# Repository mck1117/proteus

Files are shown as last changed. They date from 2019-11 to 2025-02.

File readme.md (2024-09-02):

# PROTEUS

_protean: able to do many different things; versatile._

A high-featured board compatible with [rusEFI](https://github.com/rusefi/rusefi) firmware.

TL;DR [Proteus Manual](https://github.com/rusefi/rusefi/wiki/Proteus-Manual)

# Goals and Non-Goals

## Goals

- Run my LS-swapped Volvo 240 with factory harness and equipment
- Run a sequential ignition, quad-VVT v12 engine (twelve injectors, twelve ignition, five hall sensors, four VVT actuators, dual throttles)
- Easily manufactured sealed enclosure (all connectors mount in-plane)
- ~~Extensible for knock sensing~~ properly implemented onboard knock sensing!

## Non-goals

- ~Internal logging (doesn't make sense with 12 mbit/s USB, and a sealed enclosure)~ Version 0.4 has an SD card!
- Direct injection
- Cheap

# Hardware Features

## Microcontroller

- STM32F429ZG
    - 180 MHz ARM Cortex-M7
    - 1MB flash
    - 256 KB SRAM
    - LQFP144 package

- Also fully compatible with several STM32F7 parts, including the STM32F767ZI, used on v0.1 and v0.2, as well as STM32F429ZIT6.

## Connectors
TE Connectivity AMPSEAL connectors:

- 2x 35 pin connectors
    - Board: TE 776231-1 (black, right) and 776231-2 (white, left)
    - Plug: TE 776164-1 (black, right) and 776164-2 (white, left)
- 1x 23 pin connector
    - Board: TE 776228-1
    - Plug: TE 770680-1
- 770854-1 terminals    

## Connectivity

- 1 mbit/s CAN bus
- USB 2.0 full speed (12 mbit/s), on-board or wired to connector for sealed applications
- [10-pin, 1.27mm Cortex debug header](http://infocenter.arm.com/help/topic/com.arm.doc.faqs/attached/13634/cortex_debug_connectors.pdf)

## Outputs
- 16x 4A low-side drivers
- 12x 5v ignition (or general purpose) outputs
- Dual H-bridges for electronic throttle (also supports stepper idle valve!)
- 4x 12v 3A high-side outputs

## Inputs

- 11x Analog voltage inputs
- 4x Analog temperature (5v pullup) inputs
- 2x VR crank/cam/vehicle speed inputs
- 6x hall cam/crank or digital input

## Power Supply

- Full operation from 6-24v supply
- Limited operation from 4-6v
- Dual 5v sensor supplies, 150mA each, fully protected
- Dual protected 12v external sensor supply

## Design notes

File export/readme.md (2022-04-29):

4 layer PCB

135mm x 82.5mm

[changelog.md](../changelog.md)

https://github.com/rusefi/rusefi/wiki/Hardware-Proteus-Fabrication

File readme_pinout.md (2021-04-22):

# Proteus Pinout & Wiring

### [Please use the official rusEfi Proteus docs here.](https://github.com/rusefi/rusefi/wiki/Proteus-Manual)

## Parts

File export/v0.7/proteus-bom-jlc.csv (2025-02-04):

Comment | Designator | Footprint | LCSC
Ferrite_Bead | FB1501 | Inductor_SMD:L_0805_2012Metric | C1015
8MHz | Y1501 | Crystal:Crystal_SMD_5032-2Pin_5.0x3.2mm | C115962
1k | R39,R41,R1217,R1218 | Resistor_SMD:R_0402_1005Metric | C11702
2.7k | R1101,R1102,R1103,R1104,R1201,R1202,R1203,R1204,R1401,R1402,R1403,R1404,R1405,R1406,R1407,R1408 | Resistor_SMD:R_0603_1608Metric | C13167
SM15T33CA | D1001 | Diode_SMD:D_SMC | C151281
330p | C23,C24,C905 | Capacitor_SMD:C_0402_1005Metric | C13533
10u | C18,C19,C27,C906,C1004,C1201 | Capacitor_SMD:C_1206_3216Metric | C13585
10u | L1001 | sunlord-MWSA0503:MWSA0503 | C408412
MIC4427 | U1602,U1603,U1701,U1702,U1801,U1802 | Package_SO:SOIC-8_3.9x4.9mm_P1.27mm | C20551
100n | C20,C701,C801,C901,C904,C1101,C1211,C1409,C1501,C1503,C1504,C1505,C1508,C1509,C1510,C1511,C1513,C1516,C1517,C1520,C1604,C1607,C1701,C1704,C1801,C1804 | Capacitor_SMD:C_0603_1608Metric | C14663
BTS4175SGA | U1102,U1103,U1104,U1105 | Package_SO:SOIC-8_3.9x4.9mm_P1.27mm | C152451
100n | C1,C2,C3,C4,C5,C6,C7,C8,C9,C10,C11,C12,C13,C14,C15,C16 | Capacitor_SMD:C_0402_1005Metric | C1525
33p | C1521,C1522 | Capacitor_SMD:C_0402_1005Metric | C1562
47p | C25,C26 | Capacitor_SMD:C_0402_1005Metric | C1567
1u | C1002,C1015,C1016,C1017,C1018,C1212,C1523 | Capacitor_SMD:C_0603_1608Metric | C15849
1n | C1204,C1205,C1207,C1208,C1209,C1210,C1401,C1402,C1403,C1404,C1405,C1406,C1407,C1408 | Capacitor_SMD:C_0603_1608Metric | C1588
680p | C21,C22 | Capacitor_SMD:C_0603_1608Metric | C1630
Micro_SD_Card | J1 | Connector_Card:microSD_HC_Wuerth_693072010801 | C164170
100 | R1601,R1602,R1603,R1604,R1701,R1702,R1703,R1704,R1801,R1802,R1803,R1804 | Resistor_SMD:R_0805_2012Metric | C17408
4.7k | R34,R35,R36,R37,R1205,R1206,R1208,R1209,R1210,R1211,R1213,R1214,R1215,R1216 | Resistor_SMD:R_0805_2012Metric | C17673
LMR14020 | U903 | Package_SO:SOIC-8-1EP_3.9x4.9mm_P1.27mm_EP2.29x3mm | C187824
4.7u | C30,C903,C1006,C1502,C1506,C1507,C1512,C1515 | Capacitor_SMD:C_0603_1608Metric | C19666
1k | RN201,RN202,RN301,RN302,RN401,RN402,RN501,RN502,RN1601,RN1701,RN1801 | Resistor_SMD:R_Array_Convex_4x0603 | C20197
Polyfuse | F101,F102 | Resistor_SMD:R_1206_3216Metric | C207035
120 | R33,R1004,R1106,R1108,R1110,R1112 | Resistor_SMD:R_0603_1608Metric | C22787
RED | D1504 | LED_SMD:LED_0603_1608Metric_Castellated | C2286
1 | R906 | Resistor_SMD:R_0402_1005Metric | C25086
82k | R1503 | Resistor_SMD:R_0603_1608Metric | C23254
2.2u | C1518,C1519 | Capacitor_SMD:C_0603_1608Metric | C23630
330 | R1508,R1509,R1510,R1511,R1512 | Resistor_SMD:R_0402_1005Metric | C25104
100k | R44,R45,R1501,R1901,R1902 | Resistor_SMD:R_0402_1005Metric | C25741
10k | R5,R6,R7,R8,R13,R14,R15,R16,R21,R22,R23,R24,R29,R30,R31,R32,R48,R905,R1001,R1006,R1007,R1105,R1107,R1109,R1111,R1502,R1504,R1513 | Resistor_SMD:R_0402_1005Metric | C25744
12k | R42,R43,R907 | Resistor_SMD:R_0402_1005Metric | C25752
33k | R38,R40,R46,R47 | Resistor_SMD:R_0402_1005Metric | C25779
470k | R701,R702,R703,R704,R801,R802,R803,R804,R901,R902,R903,R904,R1903,R1904 | Resistor_SMD:R_0402_1005Metric | C25790
5.6k | R1,R2,R3,R4,R9,R10,R11,R12,R17,R18,R19,R20,R25,R26,R27,R28 | Resistor_SMD:R_0402_1005Metric | C25908
10k | RN701,RN801,RN901,RN1101,RN1301 | Resistor_SMD:R_Array_Convex_4x0603 | C29718
SW_Push | SW1501,SW1502 | Button_Switch_SMD:SW_SPST_EVQQ2 | C318887
PESD1CAN-UX | D1,D2 | Package_TO_SOT_SMD:SOT-323_SC-70 | C152727
REF3333 | U8 | Package_TO_SOT_SMD:SOT-23 | C130016
2.2u | L1002 | Inductor_SMD:L_1210_3225Metric | C75646
68k | R908 | Resistor_SMD:R_0402_1005Metric | C36871
TJA1051T-3 | U6,U904 | Package_SO:SOIC-8_3.9x4.9mm_P1.27mm | C38695
3.3n | C1901,C1902 | Capacitor_SMD:C_0805_2012Metric | C53175
10n | C28,C29,C902,C1202,C1203,C1301,C1302,C1303,C1304,C1605,C1606,C1608,C1609,C1702,C1703,C1705,C1706,C1802,C1803,C1805,C1806,C1903 | Capacitor_SMD:C_0603_1608Metric | C57112
AMS1117-3.3 | U902 | Package_TO_SOT_SMD:SOT-223-3_TabPin2 | C6186
ORANGE | D1507 | LED_SMD:LED_0603_1608Metric_Castellated | C72038
BLUE | D1505 | LED_SMD:LED_0603_1608Metric_Castellated | C72041
GREEN | D1502,D1506 | LED_SMD:LED_0603_1608Metric_Castellated | C72043
MCP6002-xSN | U7 | Package_SO:SOIC-8_3.9x4.9mm_P1.27mm | C7377
USBLC6-2SC6 | U1502 | Package_TO_SOT_SMD:SOT-23-6 | C7519
MCP6004 | U5,U701,U801,U901,U1101 | Package_SO:TSSOP-14_4.4x5mm_P0.65mm | C50282
SRV05-4 | U1,U2,U3,U4,D1501 | Package_TO_SOT_SMD:SOT-23-6 | C85364
schottky | D3,D4,D1503 | Diode_SMD:D_SOD-123 | C8598
D_Schottky | D101,D102,D103,D104,D901,D903 | Diode_SMD:D_SMA | C8678
LPS25HB | U9 | Package_LGA:ST_HLGA-10_2.5x2.5mm_P0.6mm_LayoutBorder3x2y | C94049
STM32F427ZGT6 | U1501 | Package_QFP:LQFP-144_20x20mm_P0.5mm | C117816
74HC2G17 | U1202,U1207,U1208 | Package_TO_SOT_SMD:SOT-363_SC-70-6 | C10429

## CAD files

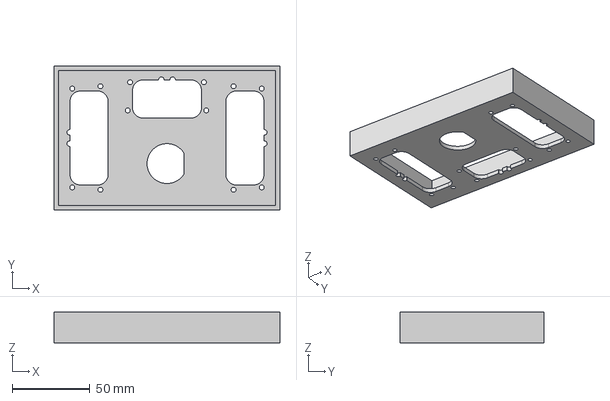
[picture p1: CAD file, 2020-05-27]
export/proteus-case.step
145.0 x 92.5 x 19.6 mm

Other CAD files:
export/Proteus_case_lid_DC-45.dwg

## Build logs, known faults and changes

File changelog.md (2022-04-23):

# Changelog

## Proteus 0.7
 - Reduce BOM lines somewhat, replacing similar components with identical components.
 - Add RTC/backup battery

## Proteus 0.6
 - Switch to TLE9202 ETB driver due to shortage of TLE9201
 - Switch to STM32F767ZG due to shortage of STM32F42x

## Proteus 0.4
 - knock sense with headset jack
 - SD card
 - USB removed from 23 pin connector

## Proteus 0.3
 - first large batch
 - incompatible pinout change mostly on the 23 pin plug

## Proteus 0.2
 - USB footprint fix

## Proteus 0.1
 - it's alive!!!

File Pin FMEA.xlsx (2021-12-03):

Pin type | Short -12v | Short GND | short <supply | Short 12v | short >supply | Tested?
5V sensor supply | E | C | n/a | C | C | case 1 smoke
12v sensor supply | E | C | B | A | A | case 1 reverse supplies main reg
Analog volt | B | A | A | B | B | yes
Analog temp | B | A | A | B | B | yes
Digital input | A | A | A | A | A | yes
VR input | C | C | C | C | C | yes
CANH/CANL | C | C | C | C | C | yes
Lowside output | E | C | C | C | C | case 1 smoke
Lowside output w/ diode | E | C | C | C | C | case 1 smoke
Ignition output | E | C | C | E | E | case 1 melted series R, case 4/5 overvolt 5v rail or melt R
High side output | C | C | C | C | E | case 5 smoke
Knock input | A | A | A | A | A | by design, no DC path
ETB | E | C | C | C | E | case 1 smoke, case 5 smoke
Ign supply (18) | C | n/a | B | A | A | yes
MR supply (23) | E | n/a | B | A | A | case 1 not allowed by TLE9201 DS

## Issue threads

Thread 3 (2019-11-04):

Should I switch to the 5v tle9471?

mck1117, 2019-11-04:
In favor of leaving it as 3.3v:
- fewer components, less board area
- potentially slightly more efficient

In favor of switching to 5v, and adding a separate 3.3v regulator:
- Potentially quieter 3.3v supply, if linear is used
- Prevents risk of 5v pull up from external shorts

mck1117, 2019-11-19:
done

Closed 2019-11-19.

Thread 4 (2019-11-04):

What do I need to control GM alternator?

mck1117, 2019-11-04:

mck1117, 2019-11-16:
Two things:
1) 12v medium current (~500mA max) field supply
2) 5v/128hz PWM current output control

mck1117, 2019-11-23:
Looks like the board has everything necessary, closing.

Closed 2019-11-23.

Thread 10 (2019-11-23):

Investigate compat with f4

mck1117, 2019-11-23:
How much has to change to also support the lqfp144 `STM32F407ZG`?

mck1117, 2019-11-23:
A first glance suggests that the pinout of of the `F767ZI` is identical to that of the `F407ZG`

mck1117, 2019-11-23:
The STM32F412 and STM32F767 nucleo boards use the same board, with a different chip installed, which suggests compatibility as well.

960, 2019-11-23:
I have used the F407 and F767 at the same boards all along, so I know for sure they are 100% compatible

mck1117, 2019-11-24:
Cool - between those data points, I think we're all set here.

Closed 2019-11-24.

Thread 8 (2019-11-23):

high side output protection

mck1117, 2019-11-23:
What needs to happen for:
- Reverse battery protection
- "ecu supply" protection (powering ECU thru high side driver)

Closed 2021-07-18.

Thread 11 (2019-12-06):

Wrong VNQ7140 footprint

mck1117, 2019-12-06:
Footprint isn't right, chip doesn't line up.

Closed 2019-12-22.

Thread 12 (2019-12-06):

Wrong BOM part for ADC protection diodes

mck1117, 2019-12-06:
BOM has diodes that are SOT323
Footprints are SOT23

Closed 2019-12-22.

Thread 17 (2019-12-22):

will the USB connector fit on the back (connector) side?

mck1117, 2019-12-22:
Or should I just add a 5x1 header for a sealed USB connector?

mck1117, 2019-12-24:
replaced connector with 5 pin 2.5mm connector for UB-20PFMP-LC7002

Closed 2019-12-24.

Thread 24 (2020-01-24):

Evaluate whether the input filter works (hint: it doesn't)

mck1117, 2020-01-24:

mck1117, 2020-01-25:
c1006 should probably be 4.7u, maybe with a 1 ohm series resistor

mck1117, 2020-03-17:
changed to 4.7u, resistor footprint added

Closed 2020-03-17.

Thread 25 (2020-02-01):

Silkscreen is important for usability

rusefi, 2020-02-01:
I believe that having silkscreen would improve usability.

Specifically silkscreen around connectors to facilitate troubleshooting & initial wiring.

mck1117, 2020-03-17:
connector silkscreen implemented on 0.3

Closed 2020-03-17.

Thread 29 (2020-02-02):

reset/boot buttons are inaccessible when installed in a case

mck1117, 2020-02-02:

mck1117, 2020-03-17:
done in 0.3 - moved to front

Closed 2020-03-17.

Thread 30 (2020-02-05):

Quantify hall input jitter & delay

mck1117, 2020-02-05:
It was pointed out that the 33k resistor may be a bit large, since that can put rise times in the 10s of us range, making us more susceptible to jitter and potentially losing short pulses altogether.

mck1117, 2020-02-11:
conclusion here: reduce series resistors to 3.3k

mck1117, 2020-02-19:
resistors changed to 3.3k, PSU investigation ongoing in #32

Closed 2020-02-19.

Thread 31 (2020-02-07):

R1002 is required for now

mck1117, 2020-02-07:
not DNP, or CAN won't work

mck1117, 2020-02-19:
changed in schematic

texasgdp754, 2020-02-23:
Noticed in mcu schematic that miso and mosi are swapped on the stm32 pins for SBC.
And miso and CSN are  swapped on hierarchal root sheet

Closed 2020-02-19.

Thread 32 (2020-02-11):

3.3v power supply noise

mck1117, 2020-02-11:
Significant noise observed on the 3.3v rail, occuring every 100us (10khz) due to the fast ADC callback waking the cpu up, causing a ~70mvpp oscillation in the 3.3v power supply.

Possible solutions:
1. Disable sleep mode on the MCU so there isn't a corresponding jump in load when it wakes up
2. Split supplies, one running the 3.3v digital, and one running VDDA, VREF+, and the digital input buffer.
3. Investigate whether the TLS205 is actually any good, or whether using a different regulator would improve performance.
4. Better isolate VREF+ (and maybe VDDA) from VDD, potentially using an RC filter for VREF+.

mck1117, 2020-02-11:
Snip from STM32F407 Discovery board schematic:
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
The capacitors circled in red are tantalum.  R23/C23/C21 creates an RC LPF, with Fc of 3.1khz, plenty low enough to suppress the 120khz ringing on VDD.

mck1117, 2020-02-11:
Example of the noise:

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

Approx 70mv peak-to-peak, ringing at ~118khz.

mck1117, 2020-03-17:
mitigated #30 by speeding up edges, added an RC filter to vref+ #34, and switched to a JLC-assembled 3.3v reg.  Will reassess with v0.3 boards in hand.

Closed 2020-03-17.

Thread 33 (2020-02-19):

r1002 should connect to 5v, not 3.3v

mck1117, 2020-02-19:

mck1117, 2020-03-17:
fixed on 0.3

Closed 2020-03-17.

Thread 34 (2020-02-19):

RC filter VREF+

mck1117, 2020-02-19:
RC filter on vref+ would do good things, ST used a 47 ohm + 1.1uf on the f4 disco board.

mck1117, 2020-03-17:
done in 0.3

Closed 2020-03-17.

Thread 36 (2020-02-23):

SPI FOR SBC CHIP

texasgdp754, 2020-02-23:
Noticed in mcu schematic that miso and mosi are swapped on the stm32 pins for SBC.
And SBC miso and sbc CSN are  connected to each other on hierarchal root sheet

mck1117, 2020-02-23:
It would appear that you are correct! I haven't tried to interface over SPI yet, so this is good to know!

mck1117, 2020-03-17:
corrected on v0.3

Closed 2020-03-17.

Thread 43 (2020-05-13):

pb2-Boot1 pin needs to be grounded

mck1117, 2020-05-13:
STM32F429 uses a different bootloader activation pattern than the F407, so not all board reliably make it to the loader when the PROG button is held.

Possible to bodge on v0.3 boards like this:
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

Closed 2020-05-13.

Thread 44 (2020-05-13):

Increase spacing on push button footprints

mck1117, 2020-05-13:
They're not easy to solder.

mck1117, 2020-05-26:
or just use JLC-assembled button, PN TS-1187A-C-D-B

rusefillc, 2020-10-10:
was this done with 0.4?

Closed 2021-07-18.

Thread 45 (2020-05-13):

Find JLC alternative for digital input buffer chip

mck1117, 2020-05-13:
It's one of the harder ones to solder.

mck1117, 2020-05-26:
74HC7014D is SO14 (wider pitch), but still not JLC assembled.

mck1117, 2020-05-26:
there are a few JLC options for dual buffer chips, part numbers 74xx2G17

mck1117, 2020-05-27:
switched to 74HC2G17GW

Closed 2020-05-27.

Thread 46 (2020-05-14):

break out SPI to 0.1" headers

mck1117, 2020-05-14:
Some adapter boards might need SPI, so make it available.

rusefi, 2020-05-25:
I would like to vote +1 for this.

Closed 2020-07-27.

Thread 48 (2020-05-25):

fix knock input impedance mismatch

mck1117, 2020-05-25:
Knock sensors are high impedance - circa 1 megaohm.

Input impedance of the frontend looks like this:
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
Something in the 3-7k ohm range.

Which means that when you include the source impedance, the filter actually does this:

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

This is neither a flat passband, nor is -42dB of gain acceptable.  That's down near the noise floor of the system, so only the loudest knocks would appear at all over the noise, and certainly not with any fidelity.

mck1117, 2020-05-25:
Something like this would probably work (further analysis required):

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

mck1117, 2020-08-28:
here's the bodge to make a v0.3 work:
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

Closed 2020-09-02.

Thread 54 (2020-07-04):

footprints instead of traces

jharvey, 2020-07-04:
There are many many footprints used instead of via's. This means you cannot use the "delete extra footprints" option under "updated PCB from schematic" tool

mck1117, 2020-11-30:
not going to try and fix before the redesign, but will do there

Closed 2020-11-30.

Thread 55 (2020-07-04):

Title block

jharvey, 2020-07-04:
The title block seems generic and the PCB does not reside within the title block boundaries. It seems odd to work off the side of the title block.

jharvey, 2020-07-04:
Also messy stuff like this on the schematic.
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

rusefillc, 2022-04-02:
Some overlap with #104 so at least two reports of same eye sore

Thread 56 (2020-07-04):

DRC / ERC

jharvey, 2020-07-04:
Several DRC and ERC errors reported. Many are "not" important, things KC wants a power flat to suppress the error things like that could be cleaned up.
-- Pin connected to.... should have power flag
-- PB2 could use nettie to suppress the message
-- Track to close to pad can be suppressed by adding a net name to the pad and making the via use that net name. AKA you really have a connected net.
-- components could be moved by like 5 mils to prevent courtyard overlap errors.

mck1117, 2020-11-03:
DRC was done in 0.4

Closed 2020-11-03.

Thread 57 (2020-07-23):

VR polarity minor mess

rusefillc, 2020-07-23:
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

mck1117, 2020-07-28:
While this wasn't intentional, with the polarity flipped, the behavior actually matches that of microRusefi.  The TLE8888 is a non-inverting setup, while the MAX992x is inverting, so flipping the pins makes them both behave the same way.

See both datasheets (TLE on top, MAX on bottom):
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

Besides, it's easy to switch the polarity in software.

So while technically wrong, I'm going to leave it wrong.

mck1117, 2020-07-28:
Comment added on the schematic explaining the logic above, with a link to this issue.

rusefillc, 2020-07-28:
Maybe a comment on the schematics confirming that this is now a feature?

Closed 2020-07-28.

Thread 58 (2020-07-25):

Proteus ETB1 MR capacitor damage

ErichPopp, 2020-07-25:
With no grounds connected to the black 23pin connector and while powered on, the black 35 pin connector was disconnected and reconnected. When it was connected again the capacitor failed and the trace between the MR pin and capacitor was vaporized.

ErichPopp, 2020-07-25:
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
![Uploading 5DC4CC11-C684-4CB4-BEEA-9F0394F303B0.jpeg…]()

mck1117, 2020-07-25:
Does the cap measure as a short circuit?

ErichPopp, 2020-07-25:
I ended up not getting back out there yesterday. It’s my birthday weekend
so I may not be out there again until Monday. I’ll let you know as soon as
I can.

On Saturday, July 25, 2020, Matthew Kennedy <notifications@github.com>
wrote:

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

mck1117, 2020-07-25:
No problem!

rusefillc, 2020-07-26:
Happy Birthday @ErichPopp!

mck1117, 2020-08-07:
@ErichPopp have a chance to test that cap?

mck1117, 2020-11-03:
I seem to remember the cap ended being a short circuit, probably due to a crack in it from the proximity to the connector.  In case it was a crack due to overvoltage (inductive spike), an electrolytic was added to the `12v_MR` net in 0.4 as extra insurance, in addition to the ceramic near each ETB driver.

Closed 2020-11-03.

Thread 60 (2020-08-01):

breakout UART pins

rusefillc, 2020-08-01:
hopefully there are a number of unused pins to breakout on the board including a pair of UART pins

this would allow external Bluetooth if gnd +3v and +5v are also available on breakout

mck1117, 2020-08-17:
done

Closed 2020-08-17.

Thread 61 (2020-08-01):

SD card provisions

rusefillc, 2020-08-01:
Looks like we are getting closer to SD card read functionality please add SD card socket on the board

47219-2001 hinge type is really easy to solder

mck1117, 2020-08-18:
SD card routed!

Closed 2020-08-18.

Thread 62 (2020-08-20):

.PDF are not searchable

rusefillc, 2020-08-20:
0.2 and 0.3 PDF schematics files are not searchable.

there are two ways to produce PDF export - kicad "PLOT" and kicad "print" + PDF printer. One way is searchable the other one is not

mck1117, 2020-08-20:
will do on 0.4

mck1117, 2020-09-02:
I think this is fixed in 0.4 schematic

Closed 2020-09-02.

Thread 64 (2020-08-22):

Is it time to enlarge?

rusefillc, 2020-08-22:
That's the case @stefanst recommends with higher chance of water tightness

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

mck1117, 2020-10-29:
dupe of #67

Closed 2020-10-29.

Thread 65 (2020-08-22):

Prototyping area

rusefillc, 2020-08-22:
How would Proteus handle Miata NB2 MAF 1k pull-down - where would it be located?

I recall there are some sensors with 12v output?

Would this case justify at least some prototyping area? I believe we can make PCB a bit larger if needed

rusefillc, 2020-08-25:
Looks like we have a lot of space on top and bottom inside the recommended case?

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

mck1117, 2020-11-03:
closed for now, will consider as part of #67

Closed 2020-11-03.

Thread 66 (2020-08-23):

Both DIR and DIS look the same on PCB viewer

rusefillc, 2020-08-23:
We have ETB1_PWM and ETB2_PWM but DIR and DIR, DIS and DIS

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

mck1117, 2020-08-24:
No idea why it does that, they all look the same on the schematic :shrug:

mck1117, 2020-11-03:
Just ctrl-click a net to highlight it, then there's no problem.

Closed 2020-11-03.

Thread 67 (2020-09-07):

Use Ferrari ECU case and connector

rusefillc, 2020-09-07:
06 2006 Volkswagen Passat 2.0L ECM ECU Engine Computer Module | 3C0 907 115 G case is available from China brand new. also used from junk yards.

crimped pigtails are available from junk yard.

would it be the simplest way to give amazing Proteus an amazing case?

rusefillc, 2020-09-07:
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

https://www.ebay.com/itm/154-pin-ECU-Connector-Bosch-Type-for-Patch-Harness-Audi-Volkswagen/333606651255

rusefillc, 2020-09-07:
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

mck1117, 2020-09-12:
154 pins is a lot - maybe some other features could get added, like integrated dumb coil drivers (igbt)

rusefillc, 2020-09-12:
is now a probability of Proteus moving in this direction?

I can make the PCB outline and card board test it in a few weeks unless we already have the outline?

rusefillc, 2020-09-26:
https://github.com/rusefi/rusefi_documentation/blob/master/oem_docs/cases/BS616%20New%20Harvard%20Cover.dwg could be the case

rusefillc, 2020-10-05:
[
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

rusefillc, 2020-11-22:
board outline https://github.com/mck1117/proteus/pull/85

mck1117, 2021-07-18:
https://github.com/mck1117/atlas

Closed 2021-07-18.

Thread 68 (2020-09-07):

Drivers with diagnostics

rusefillc, 2020-09-07:
For a nicer user experience shall we use something with diagnostics?

We have TLE6240 drivers already

rusefillc, 2020-09-07:
Is TLE8110ED the more modern version of TLE6240 ?

mck1117, 2020-09-07:
TLE9104 is an interesting option: direct control, 4 channel, spi diag

rusefillc, 2020-09-07:
TLE9104 is 3A per channel, sweet?

mck1117, 2020-09-12:
This is going to be confusing with TLE9201 and TLE9104 on the same board. Those PN are too similar!

rusefillc, 2022-04-02:
Is this more or less https://github.com/mck1117/atlas ?

mck1117, 2022-04-03:
yeah this is an atlas problem

Closed 2022-04-03.

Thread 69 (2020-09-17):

Merge Rev 0.4 cases.7z into git

rusefillc, 2020-09-17:
I assume we should have 3D cases in the same repo as PCB?

https://rusefi.com/forum/viewtopic.php?p=37857#p37857

We have a couple of alternative cases so we need some folder structure maybe by author? not sure

rusefillc, 2022-08-06:
@mck1117 poke or close? shall I merge since technically I can merge? what's your take?

rusefillc, 2022-08-17:
@mck1117 do you just totally not care? works for me. if you do not care to drop that file into the repo I definitely do not care.

Closed 2022-08-17.

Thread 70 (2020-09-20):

[0.4] unpopulated cap on PCB not on schematics

rusefillc, 2020-09-20:
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

mck1117, 2020-09-21:
Fixed in master, not going to change exports since it isn't doing any harm.  That cap was deleted from the schematic, but not removed from the layout, so it stuck around.  It's also not listed in the BOM, so no part was mounted.

Closed 2020-09-21.

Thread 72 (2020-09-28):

add rtc battery

mck1117, 2020-09-28:
add real time clock battery socket so SD logs have timestamps

rusefillc, 2021-11-08:
poke

rusefillc, 2022-04-02:
at least battery holder footprint for back side?

mck1117, 2022-04-03:
Right now it's a two pin header. I seem to remember a little battery with wires pre-soldered existed on mouser.

rusefillc, 2022-04-03:
proper fix would be to mention PN in blue right on PDF?

mck1117, 2022-04-03:
yeah I'm looking for whether this thing actually exists

mck1117, 2022-04-03:
this sort of thing exists but it's expensive https://www.amazon.com/Rome-Tech-Battery-Intel-Strix/dp/B08NZVFQRJ

rusefillc, 2023-03-23:
https://github.com/mck1117/proteus/blob/master/changelog.md#proteus-07 ?

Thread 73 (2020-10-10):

JLC fab electrolytic capacitors?

rusefillc, 2020-10-10:
microRusEFI has electrolytic capacitor populated by JLC is that possible for Proteus?

rusefillc, 2020-10-31:
is it about Anti-Vibe vs non-Anti-Vibe?

mck1117, 2020-11-03:
It's about anti vibe, and that chiniesium electrolytics have been notoriously bad in the past.  I trust Panasonic/Nichicon/etc far more than I do Lelon.

I'm actually considering instead switching to thru hole electrolytics because they're easier to solder and even sturdier than even the anti vibe SMD units.

mck1117, 2020-11-03:
potential option like PLV1H680MDL1

mck1117, 2020-11-30:
electrolytics are now thru hole, EEH-AZF1H560B and can go on either side of the board

Closed 2020-11-30.

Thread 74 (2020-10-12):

Change R1 and R2 to 0805 (or larger)

ZHoob2004, 2020-10-12:
Since these are going to be populated by users, the footprint should be for larger, more easily hand-soldered components instead of the current size.

Additionally/alternatively - could these be pre-populated with a reasonable default value without affecting mode A2 operation?

mck1117, 2020-11-03:
done in schematic, will get integrated to pcb eventually

Closed 2020-11-03.

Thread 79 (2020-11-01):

too many sources of pinout

rusefillc, 2020-11-01:
we have https://github.com/mck1117/proteus/blob/master/readme_pinout.md which seems to show 0.2 pinout but not call it out?

https://github.com/mck1117/proteus/blob/master/readme_pinout.md should probably be pointing at https://github.com/rusefi/rusefi/wiki/Hardware-Proteus-Wiring-v03 so that we do not have https://github.com/mck1117/proteus vs https://github.com/rusefi/rusefi/wiki copy-pasting?

mck1117, 2020-11-03:
fixed

Closed 2020-11-03.

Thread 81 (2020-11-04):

Is FTSH-105-01-F-DV-007-K relevant for 0.4?

rusefillc, 2020-11-04:
https://github.com/mck1117/proteus/blob/master/export/v0.3/proteus_bom_mouser.csv mentions optional FTSH-105-01-F-DV-007-K

is same FTSH-105-01-F-DV-007-K relevant for 0.4?

what is the part number for relevant St-link device? any cables needed? let's document the whole story at https://github.com/rusefi/rusefi/wiki/Proteus#dev

rusefillc, 2020-11-04:
This is very related to https://github.com/rusefi/rusefi/issues/1926

Closed 2021-01-20.

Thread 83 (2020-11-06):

put the string "f4" on the board somewhere

mck1117, 2020-11-06:
too many people have been confused about whether f4 or f7 is the correct firmware to use

Closed 2020-11-30.

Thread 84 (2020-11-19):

switch to MAX9926

mck1117, 2020-11-19:
max9926 = exactly 2 * max9924, and is larger pitch so maybe easier to solder

mck1117, 2020-11-19:
inexplicably a single 9926 is cheaper than a single 9924?

rusefillc, 2022-04-02:
Please do _not_ switch right now since I've already stock piled on max9924

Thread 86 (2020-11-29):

JLC-installed buttons for reset/bootloader

rusefillc, 2020-11-29:
jlc has many TACTILE SWITCHES

what is current Proteus extended component count?

OrchardPerformance, 2020-11-29:
Bad news is, it's likely to already be maxed out.
(the good news is, there is no more bad news?)

rusefillc, 2020-11-29:
offtopic: do we have an explicit list of extended parts currently used on Proteus?

mck1117, 2021-07-18:
done long ago

Closed 2021-07-18.

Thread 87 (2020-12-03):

2 Wire Speed Sensor Support

SVeilleux9, 2020-12-03:
Support for 2 wire speed sensors would only require a simple schematic. Simplest of schematics would be a 50 Ω low side resistor and an op-amp or Schmidt trigger to switch at ~10.5 mA. If "big proteus" has the IO supporting at least 4 - 2 wire speed sensors would be helpful for wheel speed sensors and transmission sensors.

SVeilleux9, 2020-12-03:
A popular 2 wire speed sensor that came out recently can be found here. https://www.allegromicro.com/en/products/sense/magnetic-speed/wheel-speed-sensor-ics/a19302

This part shows 2 popular protocols, Pulse Width and AK. There is a third popular protocol called "speed" which is slightly different which is described in this datasheet https://www.allegromicro.com/en/products/sense/magnetic-speed/wheel-speed-sensor-ics/ars19200

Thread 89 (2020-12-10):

LEDs

rusefillc, 2020-12-10:
the M73 starter / Passat injectors wrong pin state recent bug proves the importance of LEDs

it would be great if BigProteus had LEDs on VR inputs and all low side outputs at least, maybe more

Closed 2022-08-17.

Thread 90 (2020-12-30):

main readme.md broken link

rusefillc, 2020-12-30:
http://infocenter.arm.com/help/topic/com.arm.doc.faqs/attached/13634/cortex_debug_connectors.pdf is a broken link

Closed 2022-08-17.

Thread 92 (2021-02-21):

s/rusEfi/rusEFI/ on silkscreen

rusefillc, 2021-02-21:

mck1117, 2022-04-02:
where is it rusEfi?

mck1117, 2022-04-02:
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

OK found it, fixed now!

Closed 2022-04-02.

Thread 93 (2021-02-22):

VNLD5160 and BTS4175SGA and TLS115  no avilable at all

NoTwixD, 2021-02-22:
44 weeks on mouser
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

NoTwixD, 2021-02-22:
VN7 series are only single channel in so-8 Package

NoTwixD, 2021-02-22:
VNLD5090-E more expensive higher Drain current up to 13 A (yehh i know its overkill) lower On resistance 160>80mOhm its mean less heat ;)

NoTwixD, 2021-02-22:
and one older VNS3NV04DP-E not plug and play

NoTwixD, 2021-02-22:
same story with BTS4175SGA

NoTwixD, 2021-02-22:
I belive the tls115 i last one realy missing part of proteus at the moment

mck1117, 2021-03-28:
Yes, the 5090 is interchangeable with the 5160, and while it does dissipate less heat, the current limit is also higher (which you may or may not want).

BTS4175 is interchangeable with the BSP762 and ISP762.

mck1117, 2021-03-28:
The world is having a silicon shortage right now, so this isn't really a Proteus issue.  It's just going to be a mess for a while.

Closed 2021-03-28.

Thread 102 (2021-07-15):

Proposal to route USB signals to 776231-2

kjngineering, 2021-07-15:
I think it makes sense to give the option to route the USB signals to the white AMP connector.
Replacing the (un-needed) grounds at pins 1-4.

This would allow a simpler installation and the end user to choose where the USB port goes in installs where the ECU might not be easily accessible, as well as simplifying case design.

Would allow use of cables such as: https://www.digikey.com.au/product-detail/en/stewart-connector/67U2BD-003-K/380-67U2BD-003-K-ND/14300408

Which might lead to useful mounting for USB stick logging etc.

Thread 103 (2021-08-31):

components on BOM but not in POS

rusefillc, 2021-08-31:
C203,C204,C301,C302,C303,C304,C401,C402,C403,C404,C501,C502,C503,C504 and D101,D103 on BOM, but we couldn't find them on PNP file.

rusefillc, 2021-08-31:
Looks like some or all of these are on the back side of the board?

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

rusefillc, 2021-08-31:
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

rusefillc, 2021-09-03:
@mck1117 poke :)

rusefillc, 2021-09-04:
@mck1117 says totally fine not to populate stuff on the back "I couldn't detect a difference without those"

Closed 2022-08-17.

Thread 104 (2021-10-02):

Schematics note which diodes are usually populated which ones are not

rusefillc, 2021-10-02:
Schematics shows

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

looking it seem like proteus has 4 diodes. In reality two diodes on top side D102 D104 are always populated while two diodes on the back D101, D103 are pretty much always NOT populated

let's a have a note of that on the schematics?

rusefillc, 2022-04-02:
also text all over text is an eye sore

mck1117, 2022-04-03:
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

What if we just fit all 4 instead :)

rusefillc, 2022-04-03:
off topic:

I have sad news for you RE

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

Closed 2022-07-07.

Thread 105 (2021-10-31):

0.4 unit not powering up from +12v IGN

rusefillc, 2021-10-31:
I believe I have a damaged Proteus 0.4 board

I apply +12v on IGN pin 18, I have GND and I do not get +5

@qwerty-off suggested that I check voltage on the huge diode (?)

I have +12 on one side of huge D but not on the other

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

do we suspect damaged huge D? how would that happen?

Qwerty-OFF, 2021-10-31:
My mistake. we should check this diode
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

rusefillc, 2021-11-01:
both 12v points measure +12 - both left side of diode from top pic and right side of capacitor

right side of inductor is a huge LOL: applying "voltage" mode DMM there TURNS ON STM32. and measures +5v

rusefillc, 2021-11-01:
Adding solder on both sides of inductor has resolved this issue

this 0.4 is from Jan 2021 batch when JLC did not populate inductors

Closed 2021-11-01.

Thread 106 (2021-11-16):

chip shortage: High Side Power Switch

rusefillc, 2021-11-16:
The BTS4175SGA on U1102,U1103,U1104,U1105, also the BSP762, ISP752, ISP762 all out? what do we have for high side?

rusefillc, 2021-11-23:
I mean $9.842 is not great extra $24 per board.

I guess we can live with extra $24 per board :(

rusefillc, 2022-04-14:
@mck1117 what about VN5E010MH?

rusefillc, 2022-08-06:
@mck1117 can you please confirm/approve ISP762TFUMA1 as high-side?

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

rusefillc, 2022-08-10:
i guess https://rusefi.com/forum/viewtopic.php?p=41540#p41540 is the best confirmation available

Closed 2022-08-17.

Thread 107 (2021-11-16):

chip shortage: LINEAR VOLTAGE REGULATOR

rusefillc, 2021-11-16:
TLS115D0EJXUMA1  only available for huge MOQ, do we have alternatives?

Qwerty-OFF, 2021-11-22:
TLS115B0EJXUMA1
Similar, but without PG output
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

rusefillc, 2021-11-22:
thank you @Qwerty-OFF I've placed the order

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

rusefillc, 2021-11-24:
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

rusefillc, 2021-12-01:
hellen has a somewhat similar drama with https://www.mouser.com/ProductDetail/Texas-Instruments/LMR14020SSQDDAQ1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

are those compatible or not?

mck1117, 2021-12-01:
unfortunately not really related - TLS115 is for the sensor supplies, and Proteus ALSO has an LMR14020 for the main supply.

rusefillc, 2021-12-03:
Mouser has shipped
I've also ordered 386 of TLS115D0EJXUMA1

rusefillc, 2021-12-03:
See also https://github.com/andreika-git/hellen-one/issues/119

rusefillc, 2022-04-02:
I have a pile of both TLS115  and LMR14020

Closed 2022-04-02.

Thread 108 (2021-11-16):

chip shortage: low side

rusefillc, 2021-11-16:
BM2LC105FJ-CE2 is also out of stock now :(

BM2LB300FJ-CE2 1.7A is that acceptable?

rusefillc, 2021-11-22:
https://www.verical.com/pd/rohm-semiconductor-switch-BM2LC105FJ-CE2-6997726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

Closed 2022-08-17.

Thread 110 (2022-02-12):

CAN schematics usability

rusefillc, 2022-02-12:
can 2 in opposite corners is scary and confusing

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

rusefillc, 2022-04-02:
ask here is to visually move TXDCAN2 current top-right corner content down below TXDCAN region

rusefillc, 2022-08-06:
@mck1117 poke :)

Closed 2022-08-17.

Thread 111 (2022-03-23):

Haltech CAN Communication don't work

hugovw1976, 2022-03-23:
I test Haltech CAN bus Communication on Proteus f4 with firmware "rusEFI 2022.03.16.proteus_f4.1421086421" and don't work, I analize can hi and can low and if I select Haltech I can't see any message, I check with VAG and AIM protocol and the board send the correct messages, this is a software trouble not wardware.

mck1117, 2022-04-01:
please make an issue in https://github.com/rusefi/rusefi/issues, this repo is only for Proteus hardware

Closed 2022-04-01.

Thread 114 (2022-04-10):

voltage reference BOM cost

rusefillc, 2022-04-10:
At the moment REF3033  ±0.2% 75ppm/°C 3.3V SOT-23(SOT-23-3) Voltage References is used which is a $1.6 part

Is there a cheaper solution? what level of precision is needed? could it be accomplished with an adjustable reference like AZ432ANTR-E1?

https://datasheet.lcsc.com/lcsc/1810251610_Diodes-Incorporated-AZ432ANTR-E1_C84139.pdf

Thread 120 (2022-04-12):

At least one of the VR channels should be discrete vr

rusefillc, 2022-04-12:
LNG engine has VR crank and single tooth VR crank meaning 85ms drama

would be nice to avoid 85ms drama at least on one of Proteus VR channels

mck1117, 2022-04-12:
we can, see resistor config straps on the first channel

rusefillc, 2022-04-12:
Please not 0.7 ;)

mck1117, 2022-04-12:
as in, it's been there for some time now, a user can install resistors to change max9924 mode

rusefillc, 2022-04-12:
How does one configure for single tooth cam sensor?

mck1117, 2022-04-13:
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

Closed 2022-08-17.

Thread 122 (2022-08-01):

U1207 74HC2G17GW chip shortage

rusefillc, 2022-08-01:
C94189 is 74HC2G17GW,125 no more
while US-based assembly is possible it's just too darn "expensive"

74HC2G17GV,125 different package is also not available for JLC assembly

would it be possible to protect SN74LVC2G17 externally with additional JLC-assembled parts?

rusefillc, 2022-08-01:
See https://github.com/rusefi/proteus/issues/1
See https://github.com/rusefi/alphax-4chan/issues/49

mck1117, 2022-08-02:
yeah, we can go to discrete diodes + buffer

mck1117, 2022-08-02:
fixed in master, diodes already on BOM for analog inputs used to protect digital inputs

rusefillc, 2024-02-23:
> fixed in master, diodes already on BOM for analog inputs used to protect digital inputs, switched to SOT-23-6 74lvc2g17 buffers

that would be proteus 0.8 one day right? Not part of 0.7?

Closed 2022-08-02.

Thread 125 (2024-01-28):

VNLD5160 expect 5V voltage levels

dron0gus, 2024-01-28:
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
Threshold voltage may be as high as 3.5V which is not reachable with 3.3V STM32 GPIO.

rusefillc, 2024-01-28:
BM2LC105 is pin compatible and seems to officially support 3.3 threshold?

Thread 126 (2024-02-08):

proteus HW0.7v dont have suppressor diode on ETB Power input

WOOL929, 2024-02-08:
On the Proteus v0.7 board, the tle9201 power input does not have a suppressor Diode.

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

It seems that if the top pair of arms fails, then the reverse current from the throttle return could become a problem for the nodes on the 12v_MR bus?!

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

The datasheet has it.
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

Maybe it's not even a problem? I'm trying myself as a bug reporter

rusefillc, 2024-02-08:
@WOOL929 did you get some proteus damage which got you to look into this or is this just theoretical?

WOOL929, 2024-02-08:
> @WOOL929 did you get some proteus damage which got you to look into this or is this just theoretical?

not in my case.  just a theory.  in my case the culprit is c1203 and out- on the ground.  I have already fixed this.

rusefillc, 2024-02-09:
https://github.com/mck1117/proteus/issues/127

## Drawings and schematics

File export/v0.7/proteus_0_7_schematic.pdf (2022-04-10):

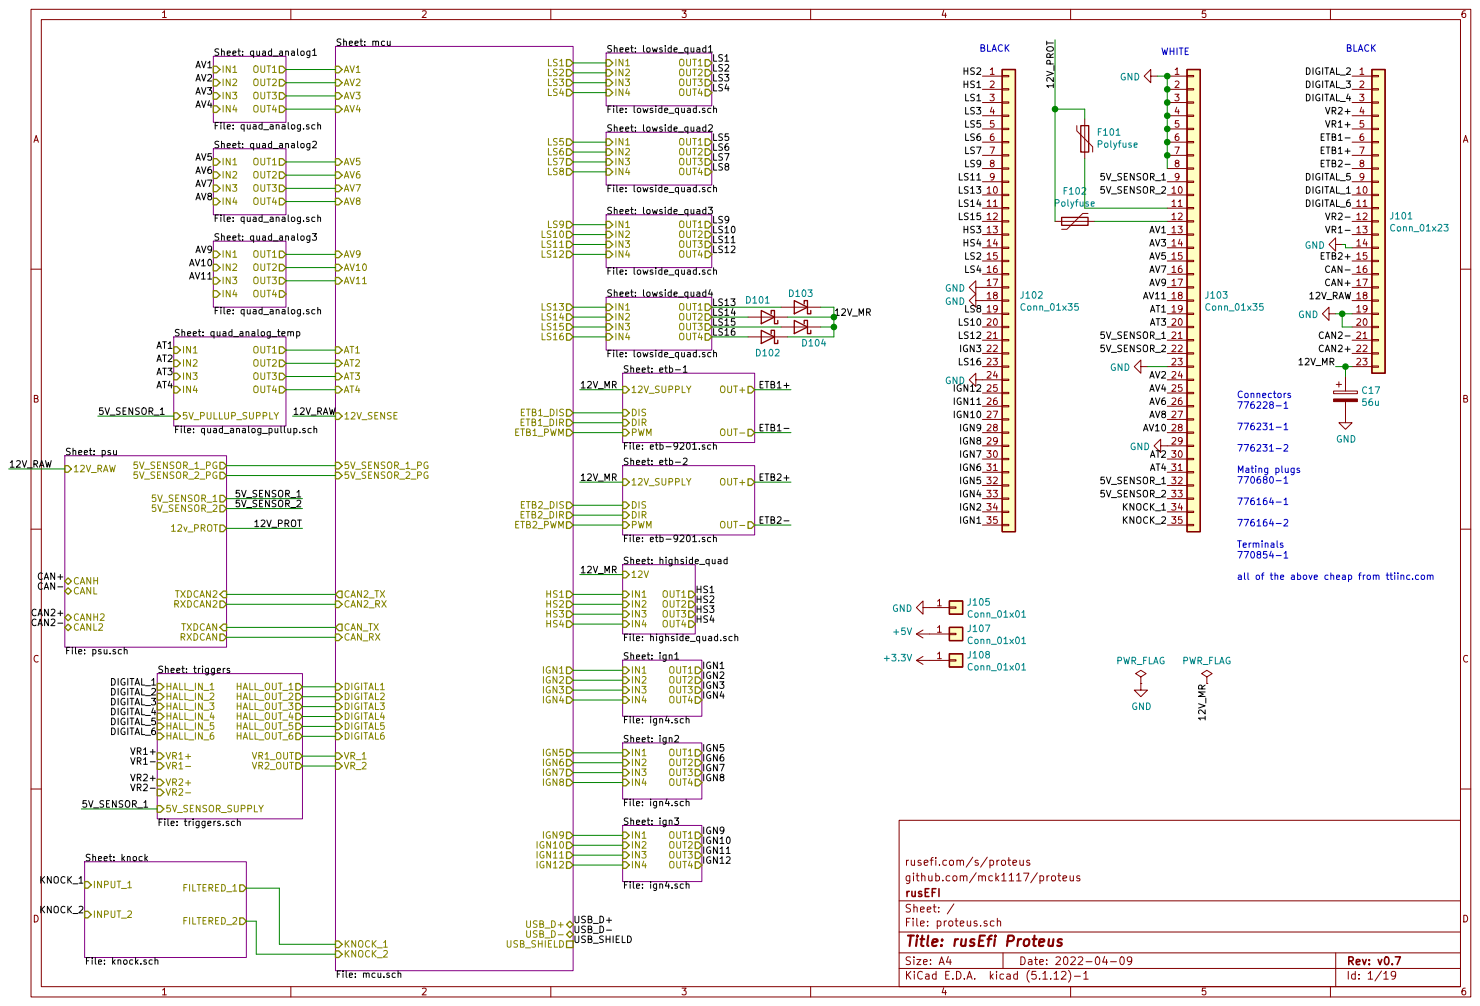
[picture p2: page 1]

all of the above cheap from ttiinc.com

rusefi.com/s/proteus
File: proteus.sch Sheet: / rusEFI github.com/mck1117/proteus

Id: 1/19 Title: rusEfi Proteus

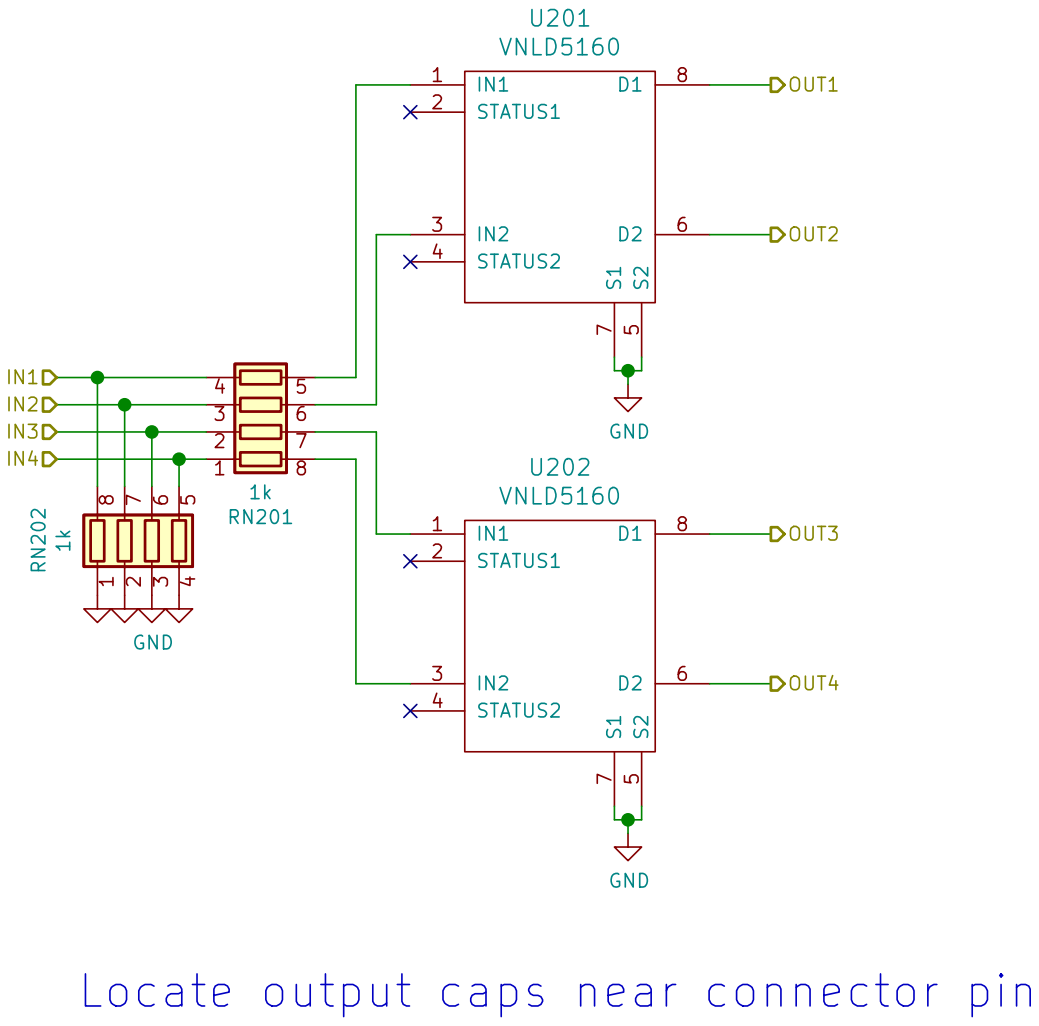
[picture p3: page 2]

rusefi.com/s/proteus
Sheet: /lowside_quad1/ rusEFI github.com/mck1117/proteus

File: lowside_quad.sch
Id: 2/19 Title: rusEfi Proteus

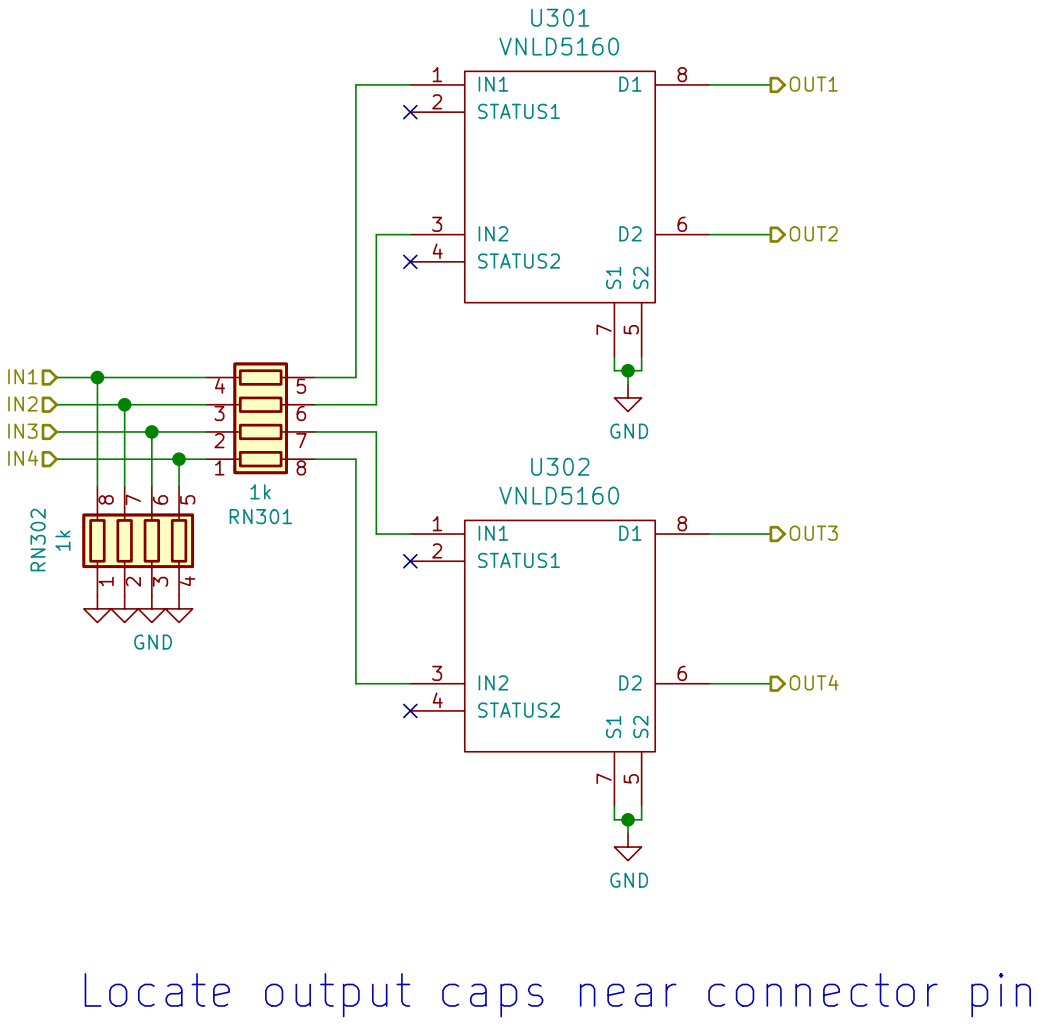
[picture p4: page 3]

rusefi.com/s/proteus
Sheet: /lowside_quad2/ rusEFI github.com/mck1117/proteus

File: lowside_quad.sch
Id: 3/19 Title: rusEfi Proteus

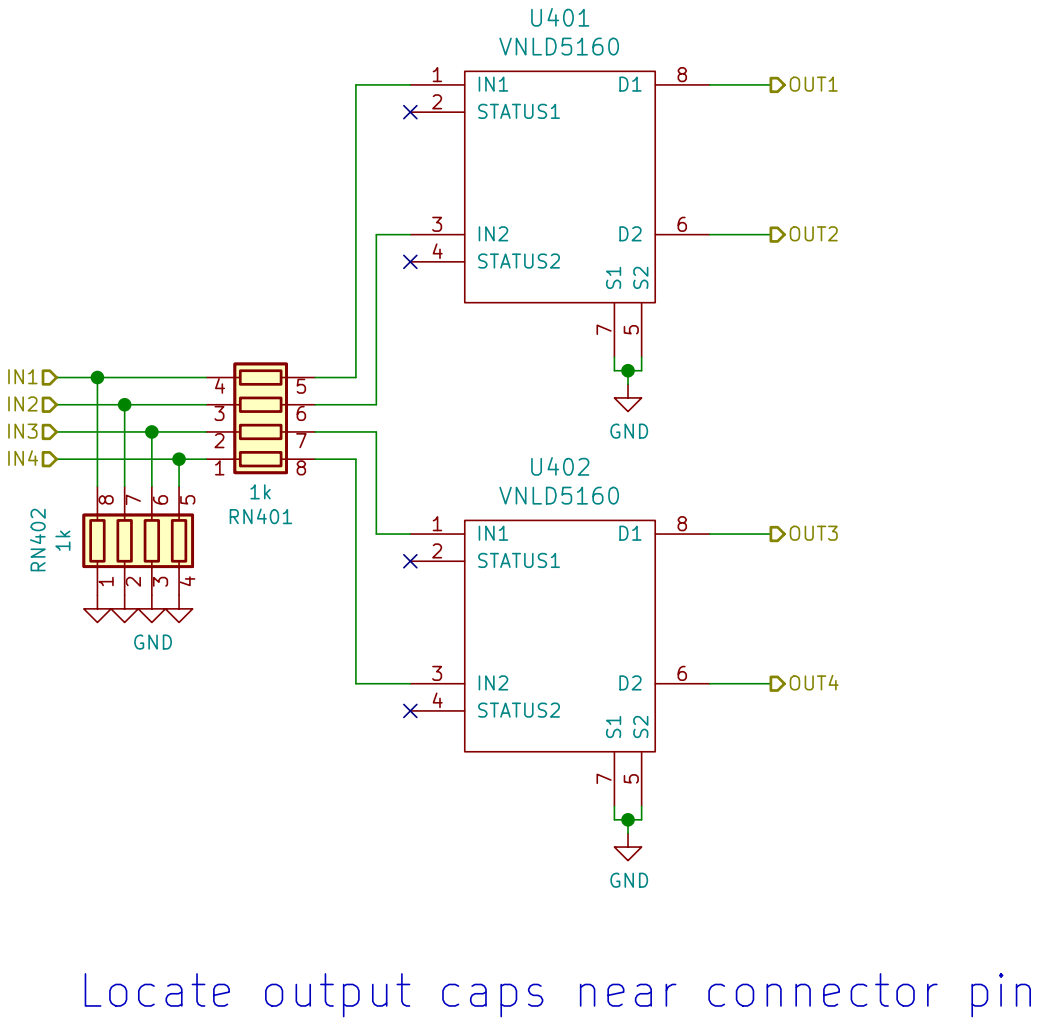
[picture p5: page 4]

rusefi.com/s/proteus
Sheet: /lowside_quad3/ rusEFI github.com/mck1117/proteus

File: lowside_quad.sch
Id: 4/19 Title: rusEfi Proteus

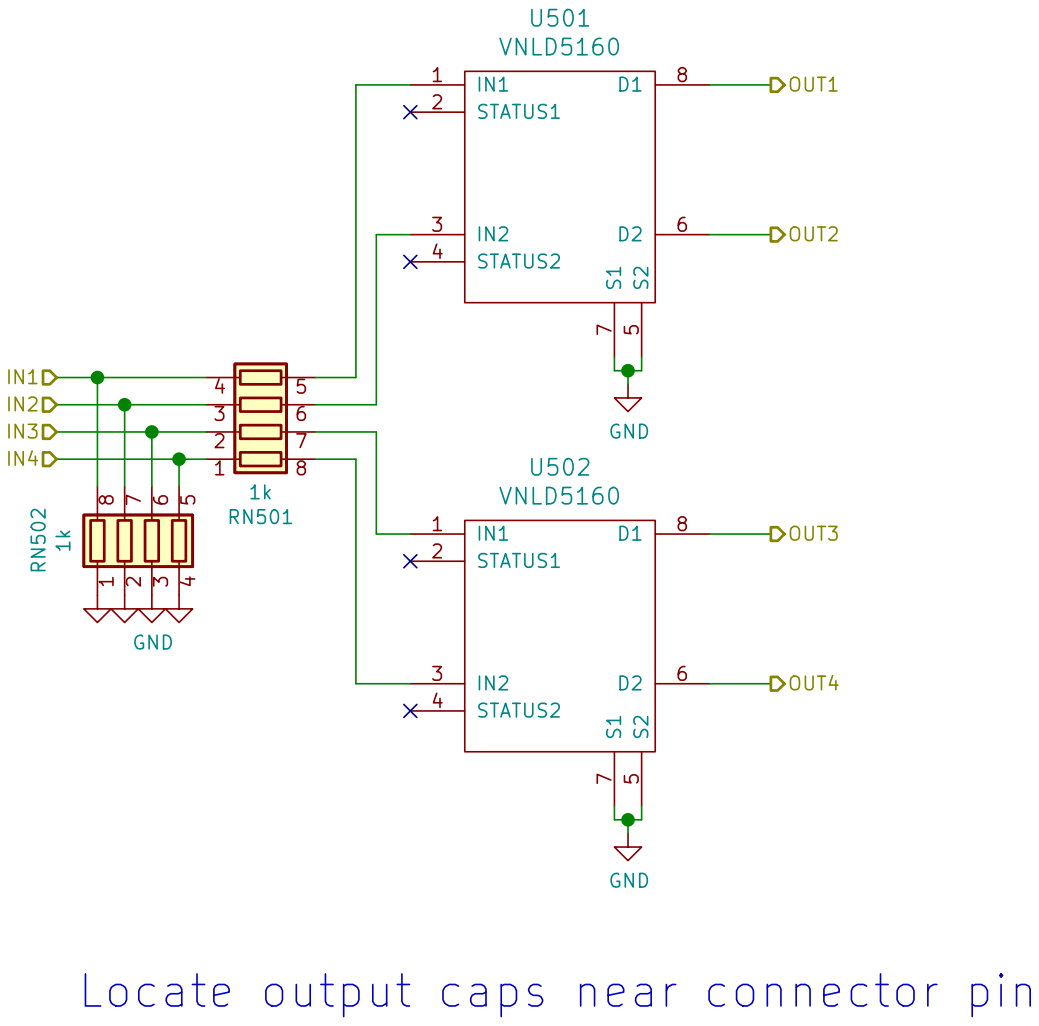
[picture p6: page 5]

rusefi.com/s/proteus
Sheet: /lowside_quad4/ rusEFI github.com/mck1117/proteus

File: lowside_quad.sch
Id: 5/19 Title: rusEfi Proteus

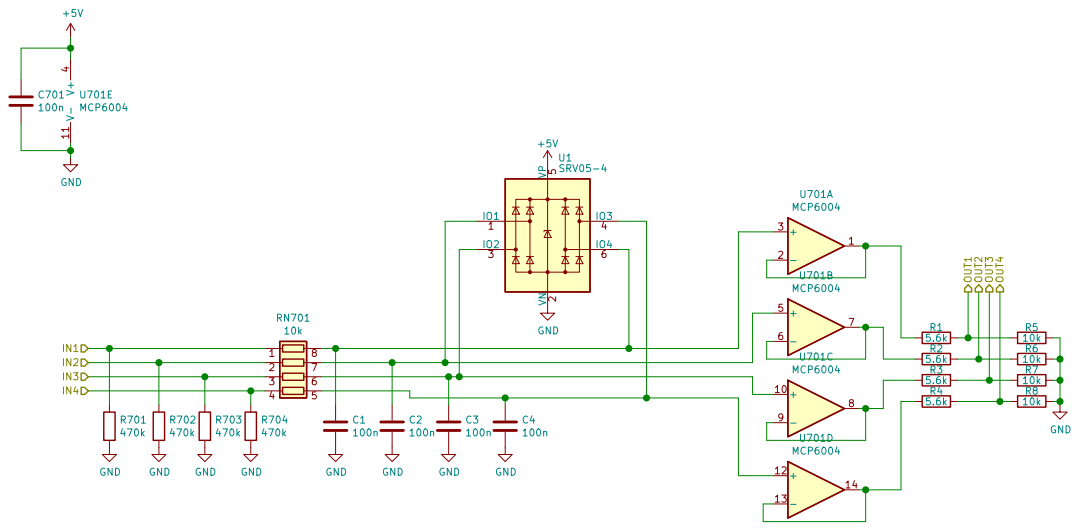
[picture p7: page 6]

rusefi.com/s/proteus
Sheet: /quad_analog1/ rusEFI github.com/mck1117/proteus

File: quad_analog.sch
Id: 6/19 Title: rusEfi Proteus

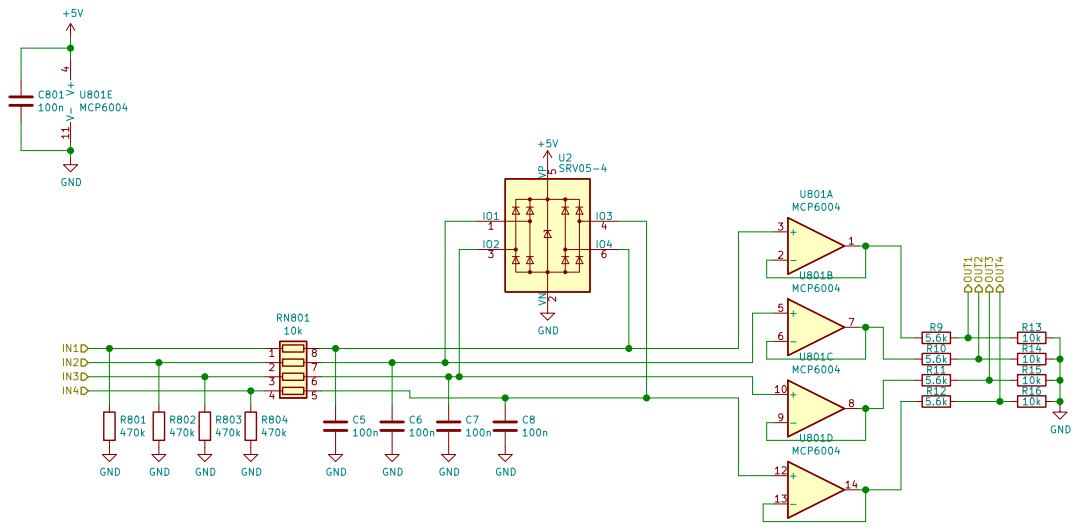
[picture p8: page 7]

rusefi.com/s/proteus
Sheet: /quad_analog2/ rusEFI github.com/mck1117/proteus

File: quad_analog.sch
Id: 7/19 Title: rusEfi Proteus

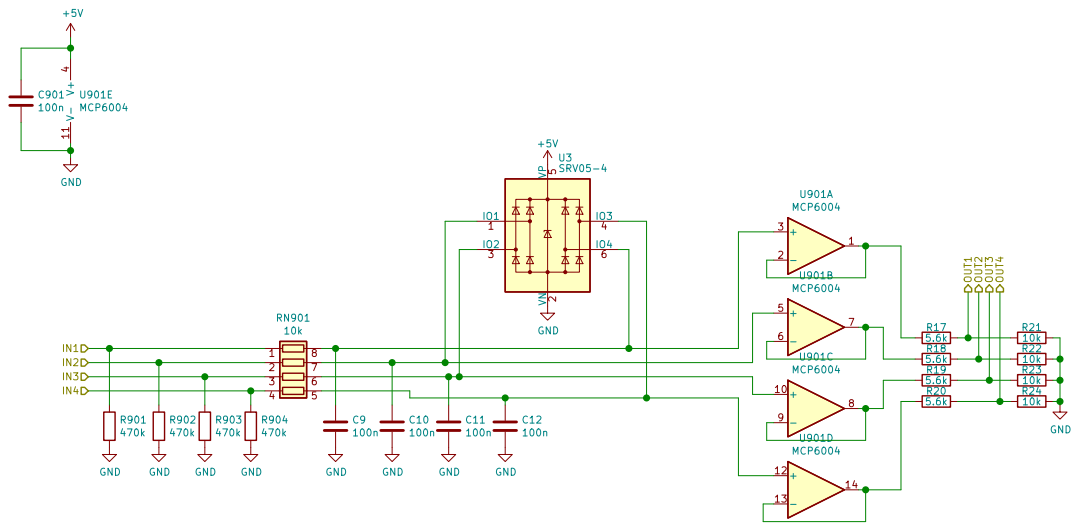
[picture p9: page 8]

rusefi.com/s/proteus
Sheet: /quad_analog3/ rusEFI github.com/mck1117/proteus

File: quad_analog.sch
Id: 8/19 Title: rusEfi Proteus

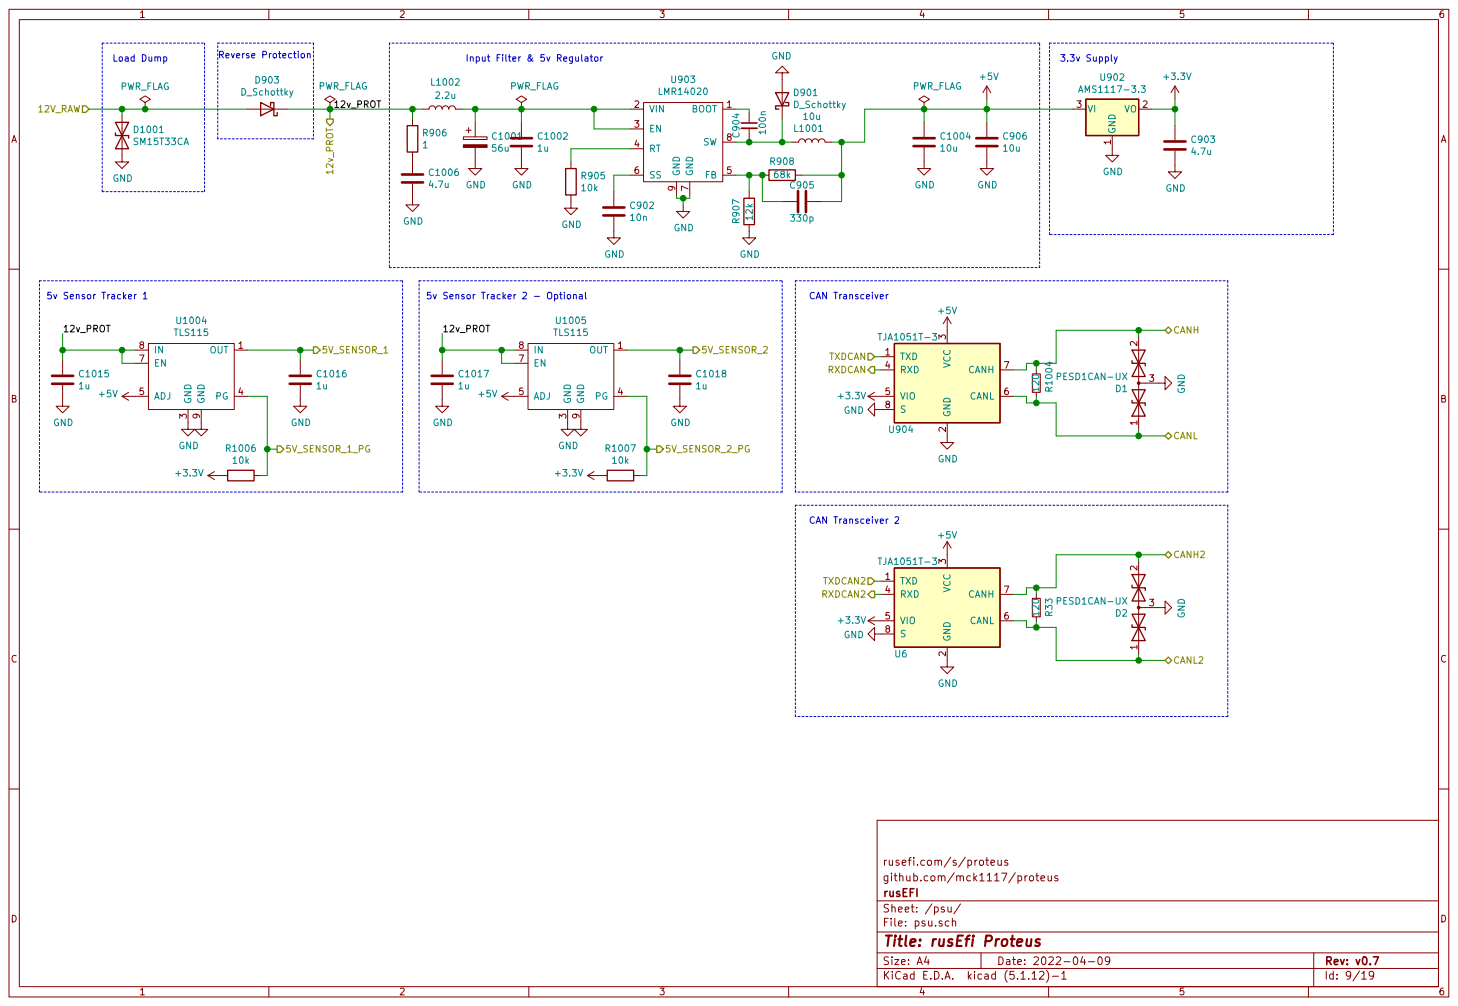
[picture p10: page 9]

3 RXD 4 VIO 5 CANL 6 CANH 7 S

rusefi.com/s/proteus
Sheet: /psu/ rusEFI github.com/mck1117/proteus

File: psu.sch
Id: 9/19 Title: rusEfi Proteus

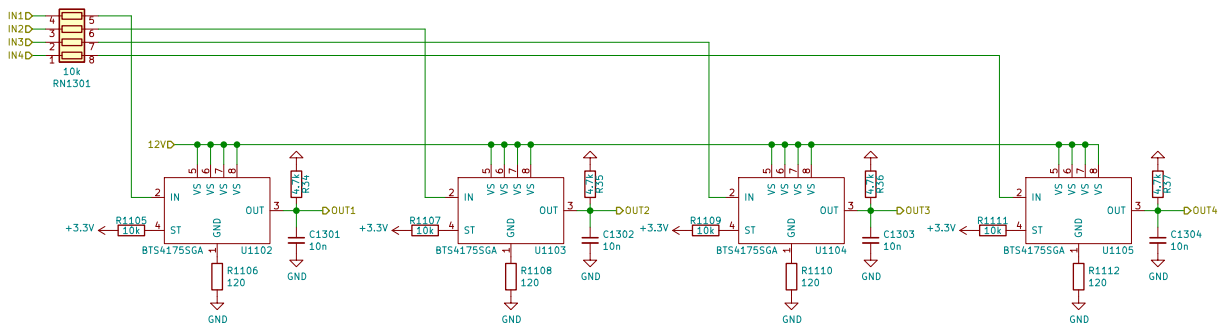
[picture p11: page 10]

Sheet: /highside_quad/ rusEFI github.com/mck1117/proteus

File: highside_quad.sch
Id: 10/19 Title: rusEfi Proteus

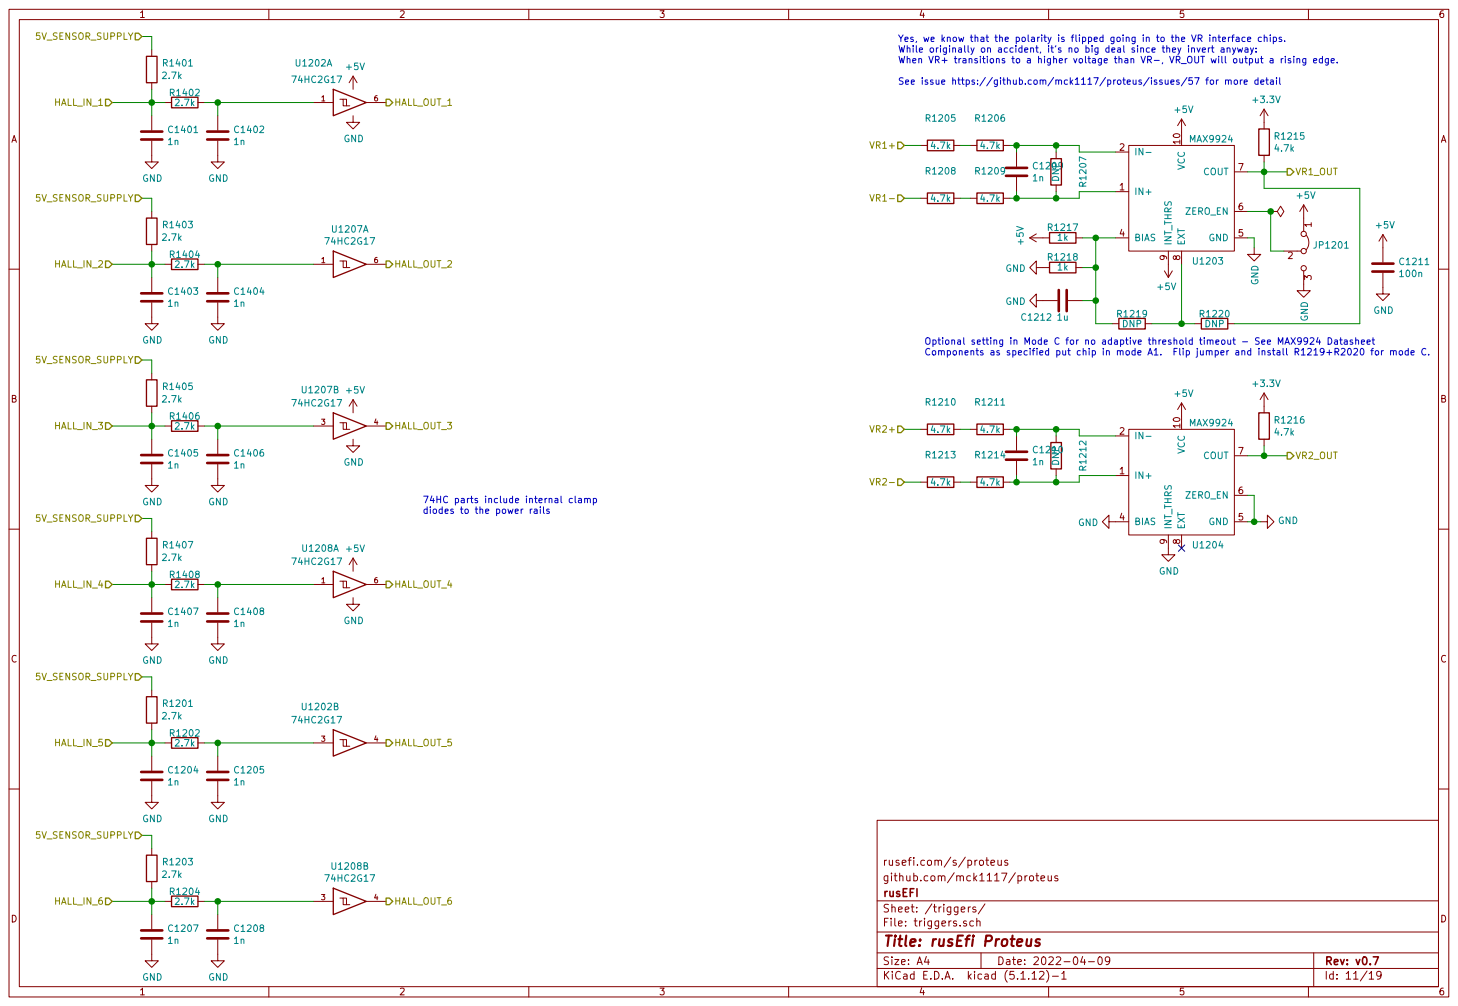
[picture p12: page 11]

Yes, we know that the polarity is flipped going in to the VR interface chips.
While originally on accident, its no big deal since they invert anyway:
When VR+ transitions to a higher voltage than VR-, VR_OUT will output a rising edge.

See issue https://github.com/mck1117/proteus/issues/57 for more detail

Optional setting in Mode C for no adaptive threshold timeout - See MAX9924 Datasheet
Components as specified put chip in mode A1. Flip jumper and install R1219+R2020 for mode C.

74HC parts include internal clamp
diodes to the power rails

Sheet: /triggers/ rusEFI github.com/mck1117/proteus

File: triggers.sch
Id: 11/19 Title: rusEfi Proteus

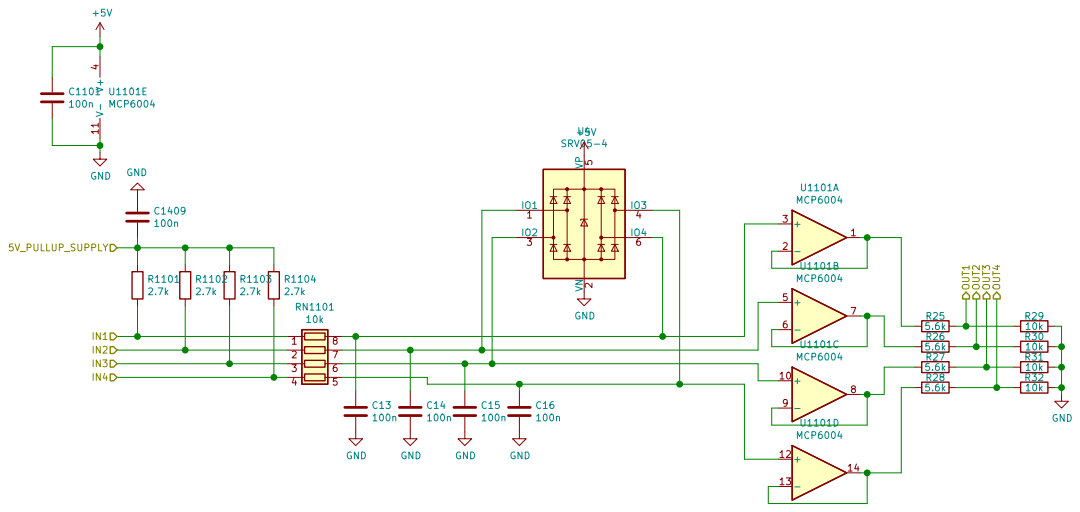
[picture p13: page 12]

Sheet: /quad_analog_temp/ rusEFI github.com/mck1117/proteus

File: quad_analog_pullup.sch
Id: 12/19 Title: rusEfi Proteus


6 VCAP_1 71 VCAP_2 106 VDD 108 VDD 131 VDD 144 VDD 17 VDD 30 VDD 39 VDD 52 VDD 62 VDD 72 VDD 84 VDDA 33 VDDSDMMC 121 VDDUSB 95 VREF+ 32 VSS 107 VSS 120 VSS 130 VSS 16 VSS 38 VSS 51 VSS 61 VSS 83 VSS 94 VSSA 31 U1501 STM32F429ZGTx +3.3V GND C1508 100n C1509 100n C1510 100n C1511 100n C1512 4.7u C1513 100n

USB Green - power Red - error Blue - comms

Tag Connect Debug Header

Pin header Connector side

1 VDD 10 SCL/SCLK 2 SDA/MOSI 4 SA0/MISO 5 CS 6

rusefi.com/s/proteus
File: mcu.sch Sheet: /mcu/ rusEFI github.com/mck1117/proteus

Id: 13/19 Title: rusEfi Proteus


rusefi.com/s/proteus
Sheet: /ign1/ rusEFI github.com/mck1117/proteus

File: ign4.sch
Id: 14/19 Title: rusEfi Proteus


rusefi.com/s/proteus
Sheet: /ign2/ rusEFI github.com/mck1117/proteus

File: ign4.sch
Id: 15/19 Title: rusEfi Proteus


rusefi.com/s/proteus
Sheet: /ign3/ rusEFI github.com/mck1117/proteus

File: ign4.sch
Id: 16/19 Title: rusEfi Proteus


rusefi.com/s/proteus
File: knock.sch Sheet: /knock/ rusEFI github.com/mck1117/proteus

Id: 17/19 Title: rusEfi Proteus


rusefi.com/s/proteus
File: etb-9201.sch Sheet: /etb-1/ rusEFI github.com/mck1117/proteus

Id: 18/19 Title: rusEfi Proteus


rusefi.com/s/proteus
File: etb-9201.sch Sheet: /etb-2/ rusEFI github.com/mck1117/proteus

Id: 19/19 Title: rusEfi Proteus

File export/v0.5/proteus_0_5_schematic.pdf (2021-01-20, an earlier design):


Sheet: etb1 File: etb.sch

all of the above cheap from ttiinc.com

rusefi.com/s/proteus
File: proteus.sch Sheet: / rusEFI github.com/mck1117/proteus

Id: 1/19 Title: rusEfi Proteus


7 D1 8 U201 VNLD5160GND GND GND GND GND GND GND

rusefi.com/s/proteus
Sheet: /lowside_quad1/ rusEFI github.com/mck1117/proteus

File: lowside_quad.sch
Id: 2/19 Title: rusEfi Proteus


7 D1 8 U301 VNLD5160GND GND GND GND GND GND GND

rusefi.com/s/proteus
Sheet: /lowside_quad2/ rusEFI github.com/mck1117/proteus

File: lowside_quad.sch
Id: 3/19 Title: rusEfi Proteus


7 D1 8 U401 VNLD5160GND GND GND GND GND GND GND

rusefi.com/s/proteus
Sheet: /lowside_quad3/ rusEFI github.com/mck1117/proteus

File: lowside_quad.sch
Id: 4/19 Title: rusEfi Proteus


7 D1 8 U501 VNLD5160GND GND GND GND GND GND GND

rusefi.com/s/proteus
Sheet: /lowside_quad4/ rusEFI github.com/mck1117/proteus

File: lowside_quad.sch
Id: 5/19 Title: rusEfi Proteus


rusefi.com/s/proteus
Sheet: /quad_analog1/ rusEFI github.com/mck1117/proteus

File: quad_analog.sch
Id: 6/19 Title: rusEfi Proteus


rusefi.com/s/proteus
Sheet: /quad_analog2/ rusEFI github.com/mck1117/proteus

File: quad_analog.sch
Id: 7/19 Title: rusEfi Proteus


rusefi.com/s/proteus
Sheet: /quad_analog3/ rusEFI github.com/mck1117/proteus

File: quad_analog.sch
Id: 8/19 Title: rusEfi Proteus


1 VO 2 VI 3 U902 AMS1117-3.3 GND GND

3 RXD 4 VIO 5 CANL 6 CANH 7 S

rusefi.com/s/proteus GND

Sheet: /psu/ rusEFI github.com/mck1117/proteus

File: psu.sch
Id: 9/19 Title: rusEfi Proteus


rusefi.com/s/proteus
File: etb.sch Sheet: /etb1/ rusEFI github.com/mck1117/proteus

Id: 10/19 Title: rusEfi Proteus


Sheet: /highside_quad/ rusEFI github.com/mck1117/proteus

File: highside_quad.sch
Id: 11/19 Title: rusEfi Proteus


Yes, we know that the polarity is flipped going in to the VR interface chips.
While originally on accident, its no big deal since they invert anyway:
When VR+ transitions to a higher voltage than VR-, VR_OUT will output a rising edge.

See issue https://github.com/mck1117/proteus/issues/57 for more detail

Optional setting in Mode C for no adaptive threshold timeout - See MAX9924 Datasheet
Components as specified put chip in mode A1. Flip jumper and install R1219+R2020 for mode C.

74HC parts include internal clamp
diodes to the power rails

Sheet: /triggers/ rusEFI github.com/mck1117/proteus

File: triggers.sch
Id: 12/19 Title: rusEfi Proteus


rusefi.com/s/proteus
File: etb.sch Sheet: /etb2/ rusEFI github.com/mck1117/proteus

Id: 13/19 Title: rusEfi Proteus


rusefi.com/s/proteus
Sheet: /quad_analog_temp/ rusEFI github.com/mck1117/proteus

File: quad_analog_pullup.sch
Id: 14/19 Title: rusEfi Proteus


USB Cortex Debug Header

6 VCAP_1 71 VCAP_2 106 VDD 108 VDD 131 VDD 144 VDD 17 VDD 30 VDD 39 VDD 52 VDD 62 VDD 72 VDD 84 VDDA 33 VDDSDMMC 121 VDDUSB 95 VREF+ 32 VSS 107 VSS 120 VSS 130 VSS 16 VSS 38 VSS 51 VSS 61 VSS 83 VSS 94 VSSA 31 U1501 STM32F429ZGTx C1516

Tag Connect Debug Header

Green - power Red - error Green - running

1 VDD 10 SCL/SCLK 2 SDA/MOSI 4 SA0/MISO 5 CS 6

rusefi.com/s/proteus
File: mcu.sch Sheet: /mcu/ rusEFI github.com/mck1117/proteus

Id: 15/19 Title: rusEfi Proteus


rusefi.com/s/proteus
Sheet: /ign1/ rusEFI github.com/mck1117/proteus

File: ign4.sch
Id: 16/19 Title: rusEfi Proteus


rusefi.com/s/proteus
Sheet: /ign2/ rusEFI github.com/mck1117/proteus

File: ign4.sch
Id: 17/19 Title: rusEfi Proteus


rusefi.com/s/proteus
Sheet: /ign3/ rusEFI github.com/mck1117/proteus

File: ign4.sch
Id: 18/19 Title: rusEfi Proteus


rusefi.com/s/proteus
File: knock.sch Sheet: /knock/ rusEFI github.com/mck1117/proteus

Id: 19/19 Title: rusEfi Proteus

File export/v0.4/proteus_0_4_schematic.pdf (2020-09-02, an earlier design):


Sheet: etb1 File: etb.sch

all of the above cheap from ttiinc.com

File: proteus.sch Sheet: / rusEfi github.com/mck1117/proteus

Id: 1/19 Title: rusEfi Proteus


7 D1 8 U201 VNLD5160GND GND GND GND GND GND GND

Sheet: /lowside_quad1/ rusEfi github.com/mck1117/proteus

File: lowside_quad.sch
Id: 2/19 Title: rusEfi Proteus


7 D1 8 U301 VNLD5160GND GND GND GND GND GND GND

Sheet: /lowside_quad2/ rusEfi github.com/mck1117/proteus

File: lowside_quad.sch
Id: 3/19 Title: rusEfi Proteus


7 D1 8 U401 VNLD5160GND GND GND GND GND GND GND

Sheet: /lowside_quad3/ rusEfi github.com/mck1117/proteus

File: lowside_quad.sch
Id: 4/19 Title: rusEfi Proteus


7 D1 8 U501 VNLD5160GND GND GND GND GND GND GND

Sheet: /lowside_quad4/ rusEfi github.com/mck1117/proteus

File: lowside_quad.sch
Id: 5/19 Title: rusEfi Proteus


Sheet: /quad_analog1/ rusEfi github.com/mck1117/proteus

File: quad_analog.sch
Id: 6/19 Title: rusEfi Proteus


Sheet: /quad_analog2/ rusEfi github.com/mck1117/proteus

File: quad_analog.sch
Id: 7/19 Title: rusEfi Proteus


Sheet: /quad_analog3/ rusEfi github.com/mck1117/proteus

File: quad_analog.sch
Id: 8/19 Title: rusEfi Proteus


1 VO 2 VI 3 U902 AMS1117-3.3 GND GND

3 RXD 4 VIO 5 CANL 6 CANH 7 S

Sheet: /psu/ rusEfi github.com/mck1117/proteus GND

File: psu.sch
Id: 9/19 Title: rusEfi Proteus


File: etb.sch Sheet: /etb1/ rusEfi github.com/mck1117/proteus

Id: 10/19 Title: rusEfi Proteus


Sheet: /highside_quad/ rusEfi github.com/mck1117/proteus

File: highside_quad.sch
Id: 11/19 Title: rusEfi Proteus


Yes, we know that the polarity is flipped going in to the VR interface chips.
While originally on accident, its no big deal since they invert anyway:
When VR+ transitions to a higher voltage than VR-, VR_OUT will output a rising edge.

See issue https://github.com/mck1117/proteus/issues/57 for more detail

Optional setting in Mode C for no adaptive threshold timeout - See MAX9924 Datasheet
Components as specified put chip in mode A1. Flip jumper and install R1219+R2020 for mode C.

74HC parts include internal clamp
diodes to the power rails

Sheet: /triggers/ rusEfi github.com/mck1117/proteus

File: triggers.sch
Id: 12/19 Title: rusEfi Proteus


File: etb.sch Sheet: /etb2/ rusEfi github.com/mck1117/proteus

Id: 13/19 Title: rusEfi Proteus


Sheet: /quad_analog_temp/ rusEfi github.com/mck1117/proteus

File: quad_analog_pullup.sch
Id: 14/19 Title: rusEfi Proteus


Green - running Blue - comms Green - power Red - error

File: mcu.sch Sheet: /mcu/ rusEfi github.com/mck1117/proteus 12
UART_RX

Id: 15/19 Title: rusEfi Proteus


Sheet: /ign1/ rusEfi github.com/mck1117/proteus

File: ign4.sch
Id: 16/19 Title: rusEfi Proteus


Sheet: /ign2/ rusEfi github.com/mck1117/proteus

File: ign4.sch
Id: 17/19 Title: rusEfi Proteus


Sheet: /ign3/ rusEfi github.com/mck1117/proteus

File: ign4.sch
Id: 18/19 Title: rusEfi Proteus


Id: 19/19 Title: File: knock.sch Sheet: /knock/





































































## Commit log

2019-10-03 add project
    [etb.sch, highside_quad.sch, ign4.sch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]
2019-10-03 route knock connector
    [lowside_quad.sch, mcu.sch, proteus.kicad_pcb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]
2019-10-03 add heatsink pad
    [etb.sch, lowside_quad.sch, mcu.sch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]
2019-10-04 route knock, cleanup
    [proteus.kicad_pcb]
2019-10-04 drc first pass
    [proteus.kicad_pcb]
2019-10-04 adc resistor divider values
    [mcu.sch, quad_analog.sch, quad_analog_pullup.sch]
2019-10-04 update pcb new values
    [proteus.kicad_pcb]
2019-10-04 route SWO
    [etb.sch, ign4.sch, mcu.sch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]
2019-10-04 wire pdr_on
    [mcu.sch, proteus.kicad_pcb]
2019-10-05 move rn501
    [proteus.kicad_pcb]
2019-10-10 add max9924
    [etb.sch, ign4.sch, lowside_quad.sch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]
2019-11-12 route 12v divided
    [mcu.sch, proteus.kicad_pcb]
2019-11-19 reroute board, use 5v not 3.3
    [etb.sch, ign4.sch, lowside_quad.sch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]
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2019-11-19 drc pass
    [proteus.kicad_pcb]
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2019-11-19 remove extra trace
    [proteus.kicad_pcb]
2019-11-20 hella vias
    [proteus.kicad_pcb]
2019-11-21 more vias
    [proteus.kicad_pcb]
2019-11-21 via/routing cleanup
    [proteus.kicad_pcb]
2019-11-21 add 12v sensor power #2
    [etb.sch, lowside_quad.sch, proteus.kicad_pcb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]
2019-11-23 leds, test pads
    [lowside_quad.sch, proteus.kicad_pcb, proteus.sch]
2019-11-23 add bootloader button
    [lowside_quad.sch, mcu.sch, proteus.kicad_pcb]
2019-11-25 BOM, fix a few footprints
    [etb.sch, highside_quad.sch, ign4.sch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]
2019-11-26 fix diodes
    [quad_analog.sch, quad_analog_pullup.sch]
2019-11-26 more part number
    [highside_quad.sch, ign4.sch, lowside_quad.sch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]
2019-11-26 minor tweaks
    [ign4.sch, lowside_quad.sch, proteus.kicad_pcb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]
2019-11-26 5090 -> 5160
    [lowside_quad.sch, proteus.kicad_pcb]
2019-11-26 fix more part numbers
    [etb.sch, ign4.sch, lowside_quad.sch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]
2019-11-27 oops wrong MCU PN
    [mcu.sch]
2019-11-27 switch inductors
    [psu.sch]
2019-11-27 add version/date
    [proteus.kicad_pcb]
2019-11-27 can ESD
    [lowside_quad.sch, proteus.kicad_pcb, psu.sch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]
2019-11-27 tall -> front
    [proteus.kicad_pcb]
2019-11-27 bootloader button -> front
    [proteus.kicad_pcb]
2019-11-27 protect usb
    [lowside_quad.sch, mcu.sch, proteus.kicad_pcb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]
2019-11-27 add part number
    [mcu.sch]
2019-11-27 fix usb protect schematic
    [mcu.sch, proteus.kicad_pcb]
2019-11-27 more part numbers
    [etb.sch, highside_quad.sch, ign4.sch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]
2019-11-27 add connector PN/color silk
    [proteus.kicad_pcb]
2019-11-28 ready to go
    [proteus.kicad_pcb]
2019-11-28 v0.1 is ready
    [proteus.kicad_pcb]
2019-12-15 fix swapped can pins, closes #14
    [mcu.sch, proteus.kicad_pcb]
2019-12-20 #11 #12 #13 issues solved
    [etb.sch, highside_quad.sch, ign4.sch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]
2019-12-22 fix rescue
    [lowside_quad.sch]
2019-12-24 add missing PowerSSO-16 footprint
2019-12-24 add second usb pinout
    [etb.sch, highside_quad.sch, ign4.sch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]
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2019-12-24 route usb header
    [lowside_quad.sch, mcu.sch, proteus.kicad_pcb]
2019-12-25 remove stray via
    [proteus.kicad_pcb]
2019-12-25 changed silk version from 0.1 to 0.2. Added JLC string for order number with JLCPCB. Created export/v0.2 folder and filled it with gerber, schematic, bom, board.
    [proteus.kicad_pcb]
2019-12-29 hide footprint labels
    [proteus.kicad_pcb]
2019-12-29 jlc recommended gerber settings
    [proteus.kicad_pcb]
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2020-01-17 tweak component values, add tolerances as req'd
    [etb.sch, highside_quad.sch, ign4.sch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]
2020-01-17 fit mcu on the page
    [mcu.sch]
2020-01-17 update title block
    [etb.sch, highside_quad.sch, ign4.sch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]
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2020-01-17 add value to max9924 pullups
    [proteus.kicad_pcb, triggers.sch]
2020-01-17 update board, ibom
    [proteus.kicad_pcb]
2020-02-19 rework start
    [proteus.kicad_pcb]
2020-02-19 revise component values
    [etb.sch, highside_quad.sch, ign4.sch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]
2020-02-20 update more values
    [psu.sch]
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2020-03-17 v0.3 progress
    [etb.sch, highside_quad.sch, ign4.sch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]
2020-04-09 0.3 progress
    [etb.sch, highside_quad.sch, ign4.sch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]
2020-04-09 fix jlc opamps
    [knock.sch, proteus.kicad_pcb, quad_analog.sch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]
2020-04-12 led resistors
    [mcu.sch]
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2020-04-13 fix pos rotations
    [proteus-top-pos.csv]
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2020-04-15 update to lmr14020, add diodes
    [etb.sch, ign4.sch, mcu.sch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]
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2020-04-15 3D for ampseal 35P (#41)
    * added 3d for 35p ampseal
    * solved some fuckery before merge
    [proteus.kicad_pcb]
2020-04-15 switch knock cap to 603
    [knock.sch, proteus.kicad_pcb]
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2020-04-16 swap to f429zg
    [ign4.sch, lowside_quad.sch, mcu.sch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]
2020-04-16 switch high side driver
    [etb.sch, highside_quad.sch, ign4.sch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]
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2020-04-16 adjust clearance
    [proteus.kicad_pcb]
2020-04-16 fix smd attribute on inductor
    [proteus.kicad_pcb]
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2020-04-16 add mode C option for VR1
    [etb.sch, lowside_quad.sch, mcu.sch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]
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2020-05-04 correct USB, rev to v0.3a
    [mcu.sch, proteus.kicad_pcb, proteus_bom_jlcpcb.csv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]
2020-05-13 ground boot1, fix #43
    [mcu.sch, proteus.kicad_pcb]
2020-05-15 fix other usb pinout
    [mcu.sch, proteus.kicad_pcb]
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2020-05-27 switch to 2g17 buffers #45
    [proteus.kicad_pcb, quad_analog.sch, triggers.sch]
2020-05-28 add SPI breakout #46
    [mcu.sch, proteus.kicad_pcb, quad_analog.sch]
2020-06-05 Modified ampseal.pretty to use new model for 23-pin connector (#51)
    [proteus.kicad_pcb]
2020-07-01 fix PN on sealed connector #53
    [mcu.sch]
2020-07-28 knock jumper, comment about VR, add MR cap
    [knock.sch, proteus.sch, triggers.sch]
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2020-08-22 add line out #59
    [etb.sch, knock.sch, mcu.sch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]
2020-08-22 fix vr naming #63
    [lowside_quad.sch, mcu.sch, proteus.sch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]
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2020-11-03 fix #77
    [proteus_bom_mouser.csv]
2020-11-03 #76 and #74 progress
    [highside_quad.sch, lowside_quad.sch, quad_analog.sch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]
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2020-12-03 big proteus outline (#85)
    [boardout.kicad_pcb, boardout.sch]
2021-01-10 fix knock phono out opamp
    [knock.sch]
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2021-01-16 baro sensor, JLC buttons, add voltage ref
    [mcu.sch]
2021-01-17 fix jlc pn
    [highside_quad.sch]
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2021-01-20 simplify 5v sensor supply routing slightly
    [psu.sch]
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2021-01-20 add qty to mouser csv
    [proteus-bom-mouser.csv]
2021-01-29 polycase case (#91)
    * polycase case
    * polycase case update
    [Proteus_case_lid_DC-45.dwg]
2021-03-27 update board text, bom
    [proteus-bom-jlc.csv]
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2022-04-03 move diodes to front
    [etb-9201.sch, highside_quad.sch, ign4.sch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]
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2022-04-11 0.7 order (#115)
    * misc details
    * April fab
    * 2022 order
    [proteus-bom-jlc.csv, proteus-bom-not-jlc.csv]
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2022-08-02 switch to SN74LVC2G17 #122
    [etb-9201.sch, ign4.sch, lowside_quad.sch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]
2022-08-02 comment explaining my sins
    [triggers.sch]
2025-02-04 correct JLC BOM line for U1202/1207/1208
    [proteus-bom-jlc.csv]
2025-02-14 update to kicad 7
    [etb-9201.kicad_sch, etb-9201.sch, etb.sch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]
